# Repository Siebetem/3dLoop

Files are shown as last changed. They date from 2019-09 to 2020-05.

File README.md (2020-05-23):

# 3dLoop
## Intro
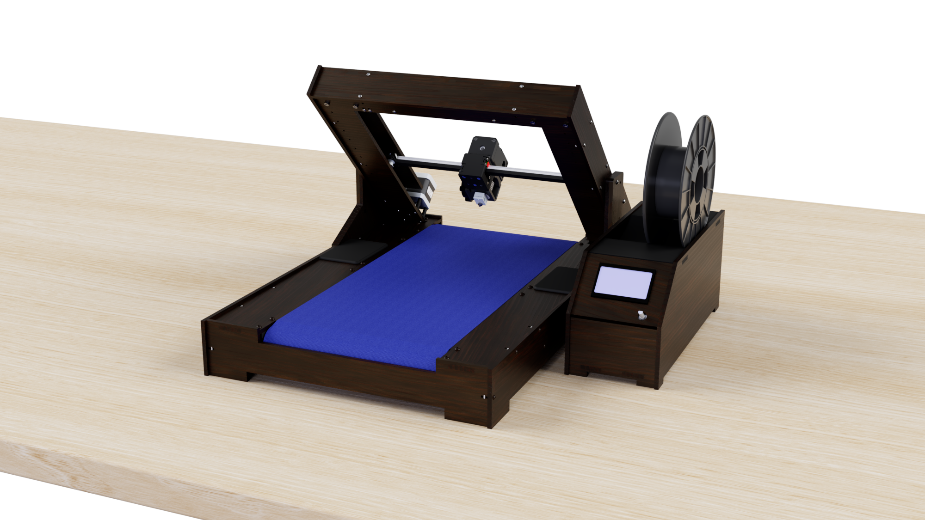
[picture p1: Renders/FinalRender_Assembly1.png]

3D printers are awesome machines, but they come with a variety of limitations:

First: printed objects are mostly small. Prints are always smaller than the printer itself. So if you want to make big prints, you need a big printer and even with this big printer are possibilities limited.

Second: When the printer is finished printing your object, human interaction is needed to proceed the next print. The printer isn’t able to remove the printed object and start a new one.

To produce parts fast and cost-effectively, I’ve designed a printer that can print many parts sequentially. Not only will it be more costeffective than other printers, it will be fairly easy to reproduce the printer with a minimal need of tools. I tried to make as many parts as possible with tools that are accessible in a FabLab/makerspace.

The printer uses a conveyor belt as print bed, whereas a normal printer uses a fixed build plate. A belt as printbed enables the printer to roll off the object and start printing a new object. This also makes it possible to make objects that are (almost) infinite in 1 direction.

There are 2 differtent configurations in which the printer can be configured.
I will describe the 2 differtent configurations separatly:

## Configuration 1 (Infinite printing)
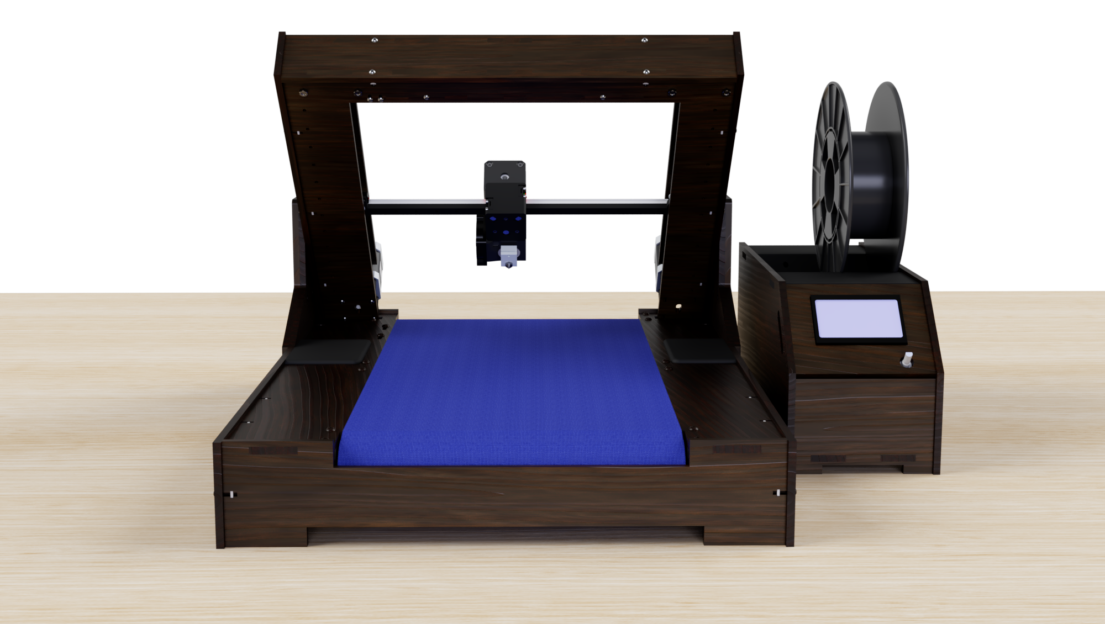
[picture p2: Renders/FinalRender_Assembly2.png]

In this configuration, It's possible to make objects with one infinite dimention.
The X,Y-assembly is oriented under an 45 degree angle towards the bed assembly.
This is especially usefull for extrusions, but it makes it also possible to print objects without support wereas normal printers would need support. For every layer, the bed system rols a bit further. In that way, objects can be bigger than the length of the belt.

## Configuration 2 (Normal 3D printer with automated object rejection)
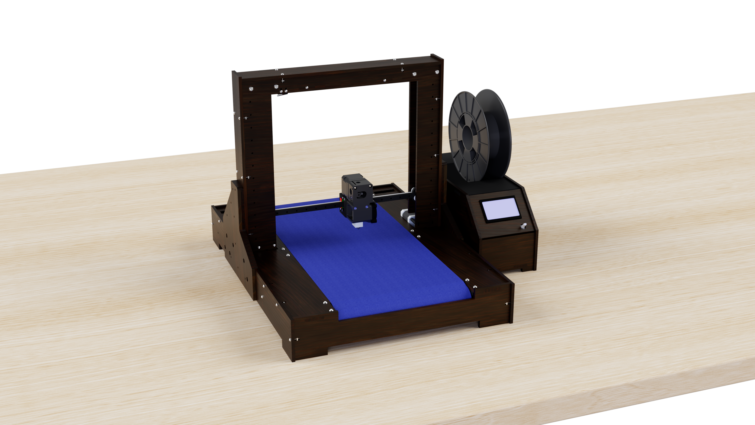
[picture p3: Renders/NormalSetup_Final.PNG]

This configuration give you all the advantages of the standard XYZ setup with the addition of automaticly rejection of the print. It makes it possible to print many objects, without the need of human interaction between diffrent objects. This is especially handy when you want to make a printfarm, or want to print many parts when you're away or sleeping.

The design makes it very easy to switch between the two configurations. The extruderassembly is magnetic detatchable. It's possible to attach the extruderassembly in 2 different orientations to the X-carriage.

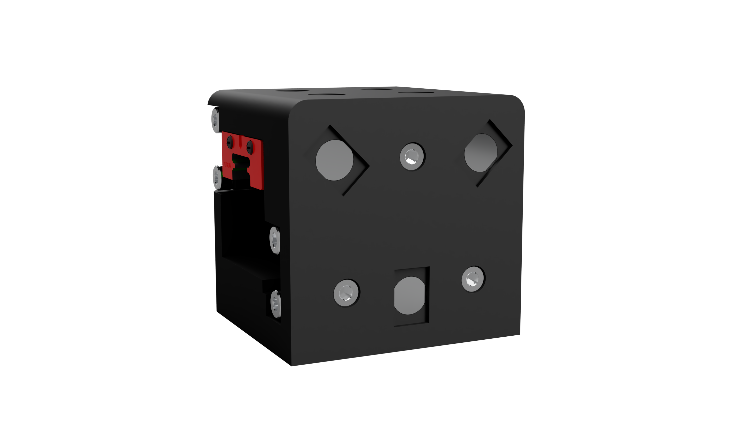
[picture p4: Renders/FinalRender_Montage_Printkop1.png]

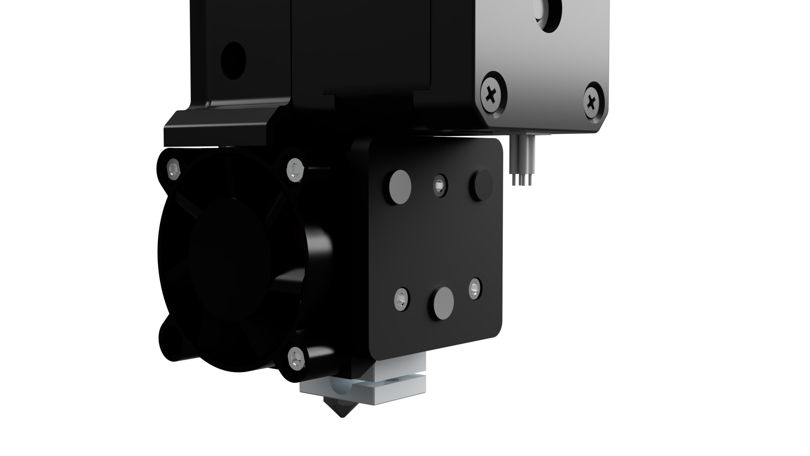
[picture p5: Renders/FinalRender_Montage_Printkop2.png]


The XY-axis assembly is easy detatchable from the Z-axis assembly by unscrewing 3 screws on each side.

By the use of two side pannels, the XY-as can be easely swichted between the two configurations. In the side pannels there are holes to mount the XY-axis vertically (Configuration 2) and under a 45 degree angle (Configuration 1).

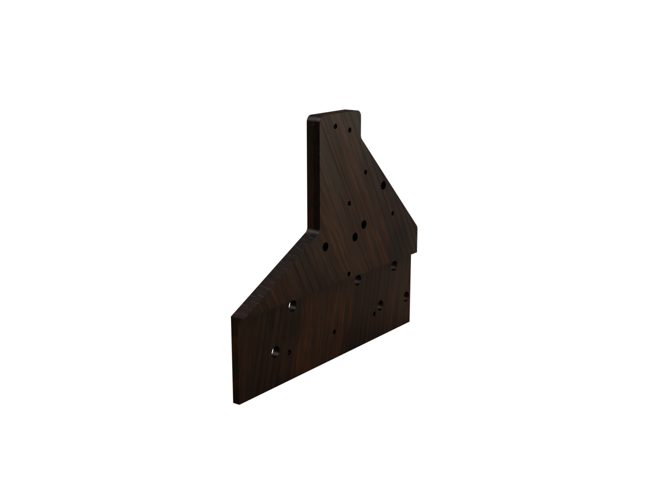
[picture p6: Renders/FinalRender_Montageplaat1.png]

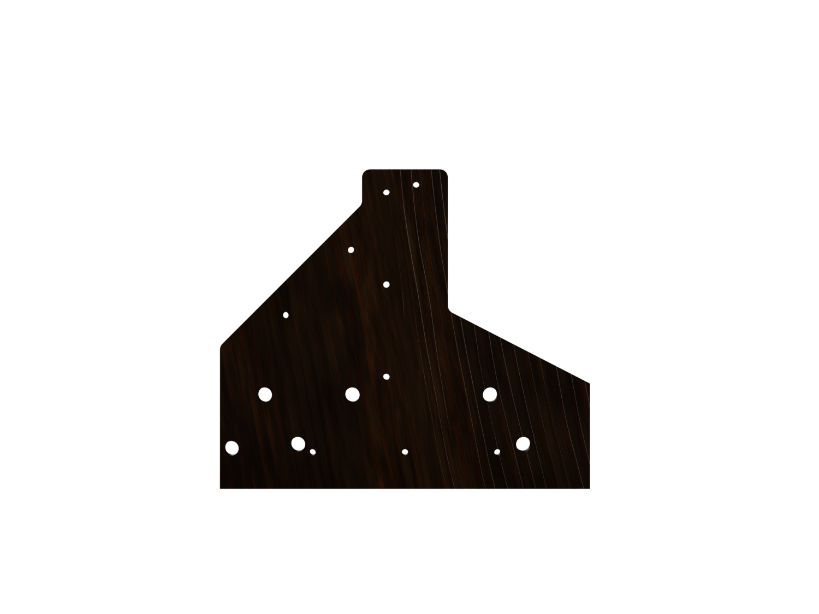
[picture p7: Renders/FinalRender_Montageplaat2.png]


## Electronic Box
The mainbord and powersupply are mounted inside a seperate unit, the electronic box.
The printer uses a MKS GEN 1.4 board, to run the Marlin firmware.
In the electronic box, there was special attention needed to the airflow, to prevent the closed box form overheating.
On the top of this box, there is a spoolholder.

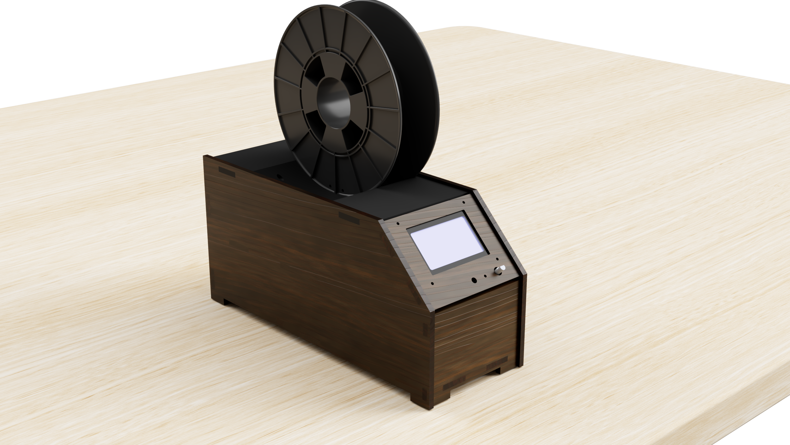
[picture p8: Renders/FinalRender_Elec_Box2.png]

On the back of the box, there are all the connectors for the differtent components. The use of connectors makes transportation of the printer easier.
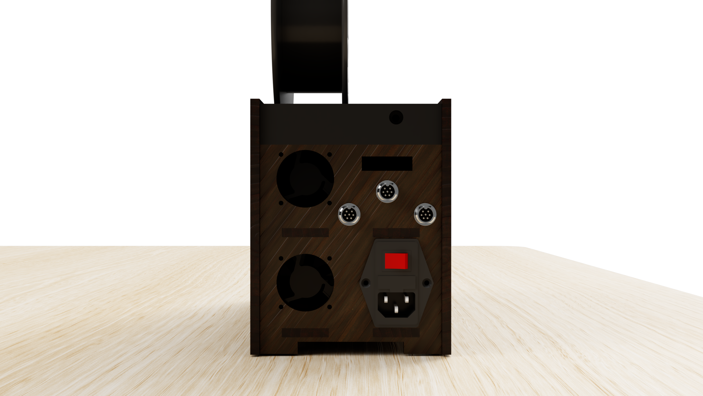
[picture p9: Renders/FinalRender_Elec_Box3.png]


##
This printer is fully custom made, every part is carefully designed to make sure the machine will work as good as possible.

On this Github page, you can find all the details about this printer. I share all the designfiles as well as software, firmware and used parts.

Don't hesitate to contact me or post a comment if you have any questions!

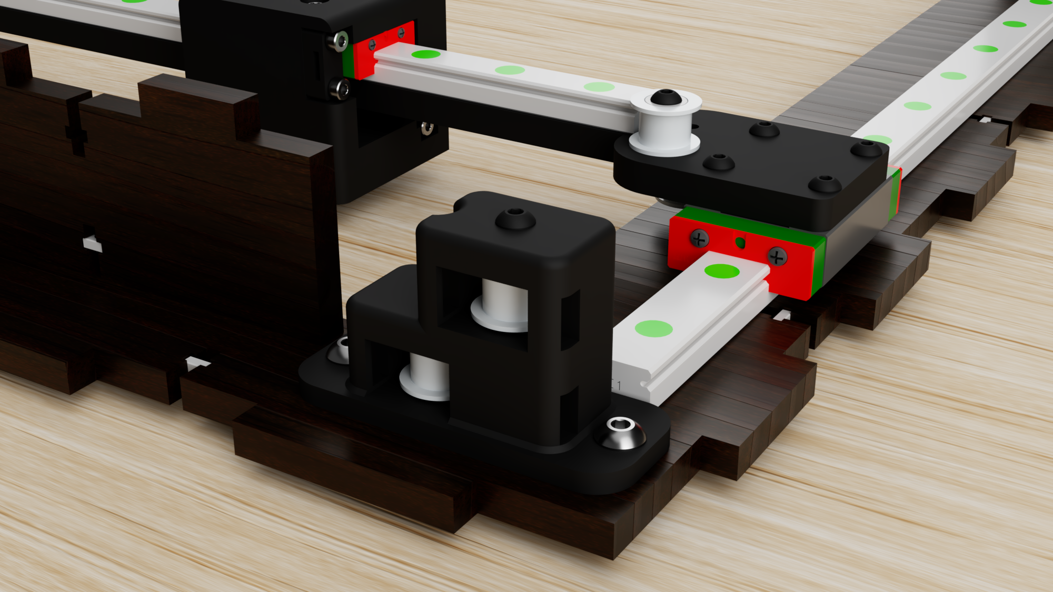
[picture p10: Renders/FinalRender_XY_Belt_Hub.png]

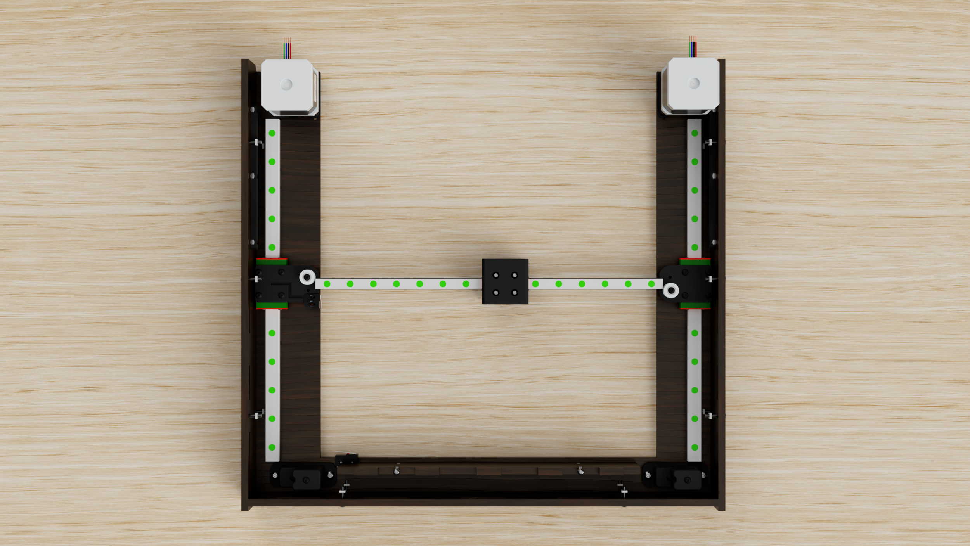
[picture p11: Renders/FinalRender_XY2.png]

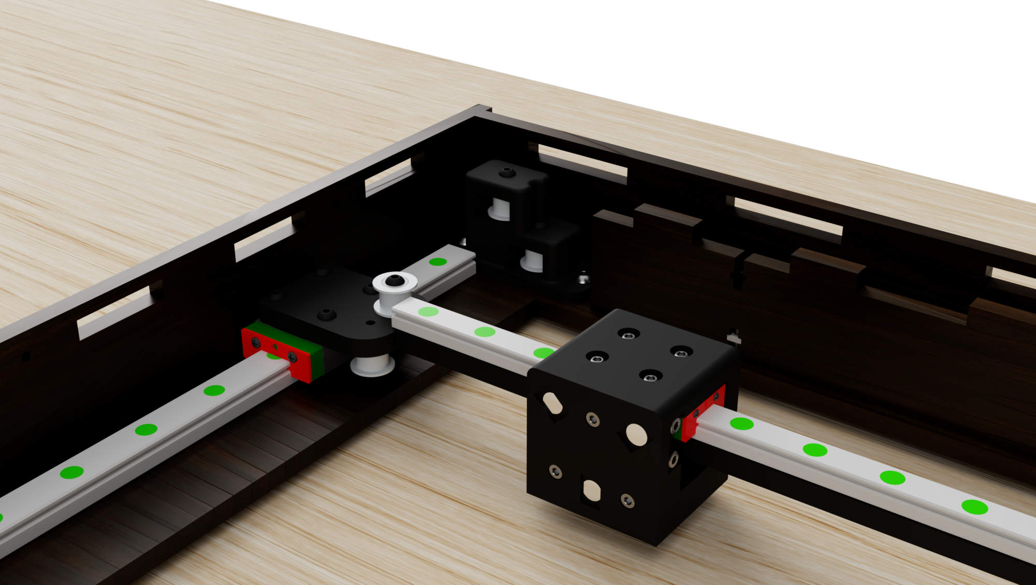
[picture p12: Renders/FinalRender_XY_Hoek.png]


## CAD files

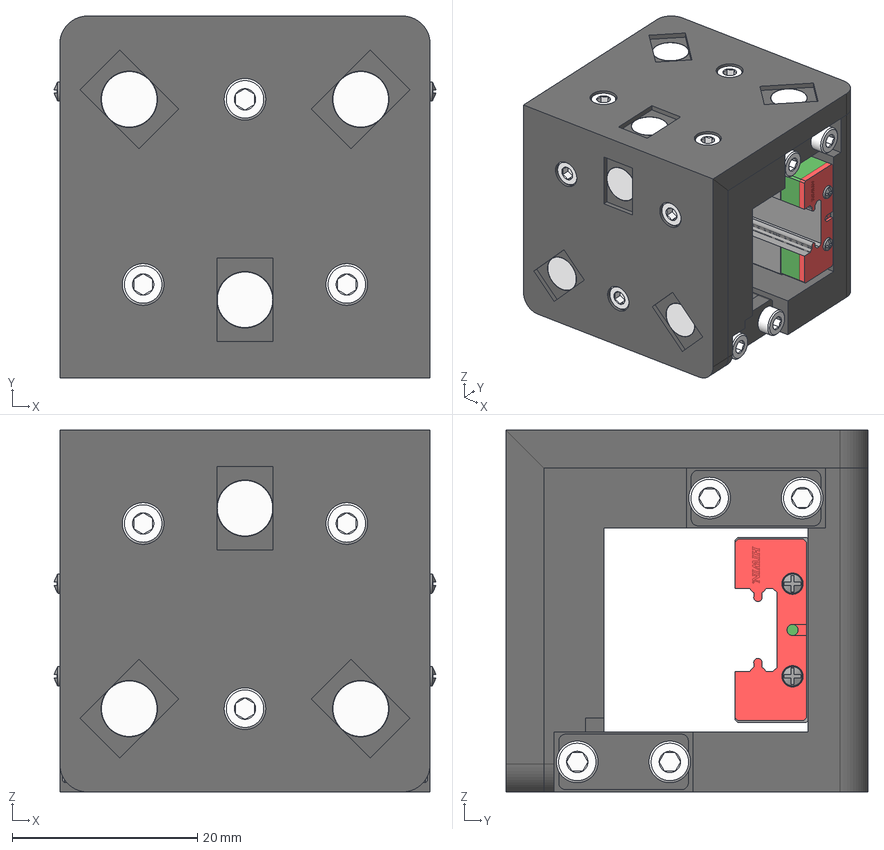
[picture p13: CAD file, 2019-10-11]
CAD_Files/3D_Files/XY-Axis/STEP_Files/Carriage_Assembly v25.step
41.3 x 39.1 x 39.1 mm
MGN09H_ZF_H_M_SS_FILE_1
Magnet x 6
M2.5x5 x 6
M2.5x10 x 8
M3x6 x 4

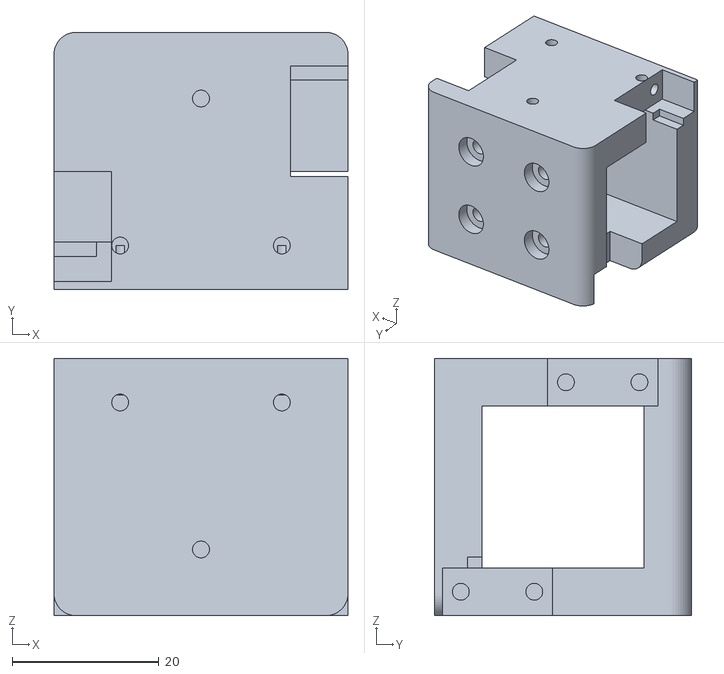
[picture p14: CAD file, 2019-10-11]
CAD_Files/3D_Files/XY-Axis/STL_Files/Carriage_Assembly v26.stl
40.0 x 35.0 x 35.0

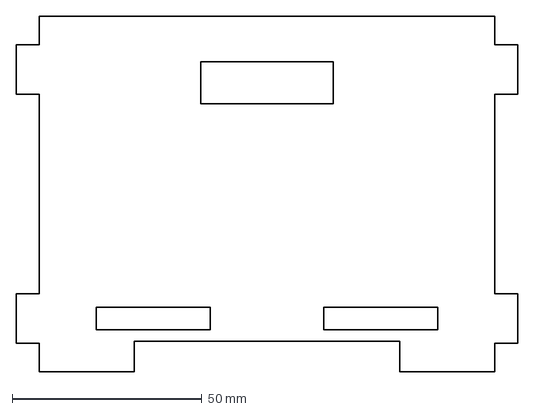
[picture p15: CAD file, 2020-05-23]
CAD_Files/2D_Files/ControllerBox/ControllerBox_Front_SD.dxf
132.0 x 93.6 mm

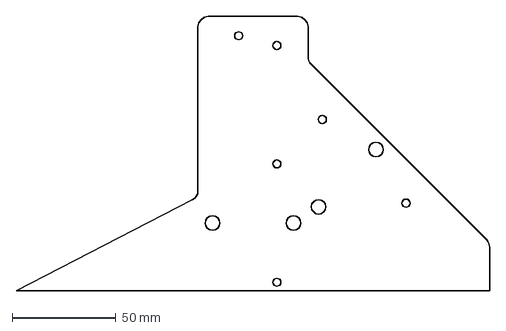
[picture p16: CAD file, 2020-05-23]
CAD_Files/2D_Files/MountingPlate/MountingPlate2.dxf
228.0 x 132.0 mm

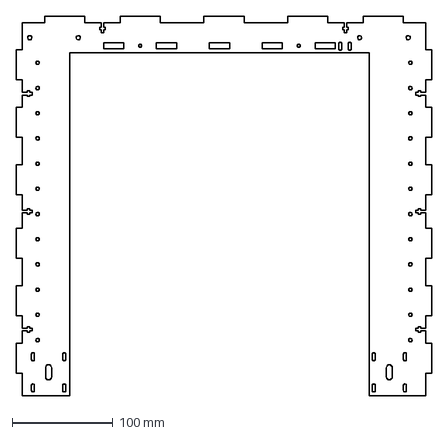
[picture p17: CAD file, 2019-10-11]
CAD_Files/2D_Files/XY-Axis/XY-Axis_Bottem.dxf
412.0 x 376.0 mm

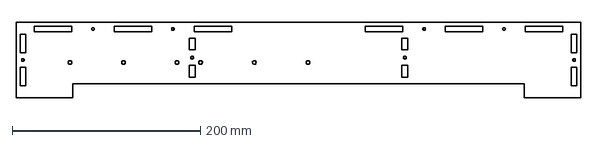
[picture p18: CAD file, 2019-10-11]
CAD_Files/2D_Files/Z-Axis/Z-Axis_Bed_Side.dxf
600.0 x 80.0 mm

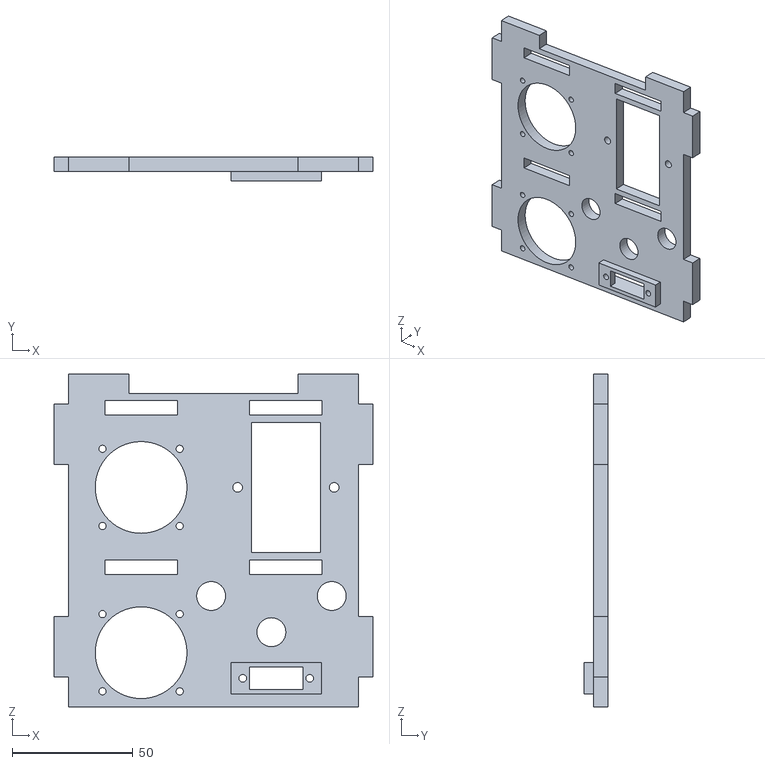
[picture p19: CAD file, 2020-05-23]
CAD_Files/3D_Files/ControllerBox/Back.stl
132.0 x 10.0 x 138.0

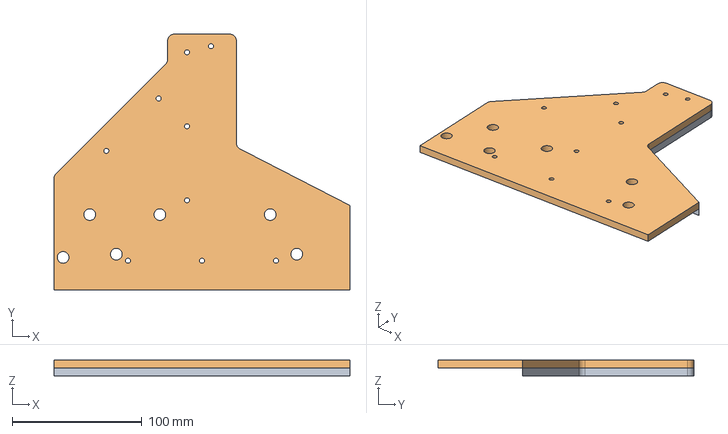
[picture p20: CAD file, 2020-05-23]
CAD_Files/3D_Files/MountingPlate/MountingPlate_v37.step
228.0 x 197.0 x 12.0 mm

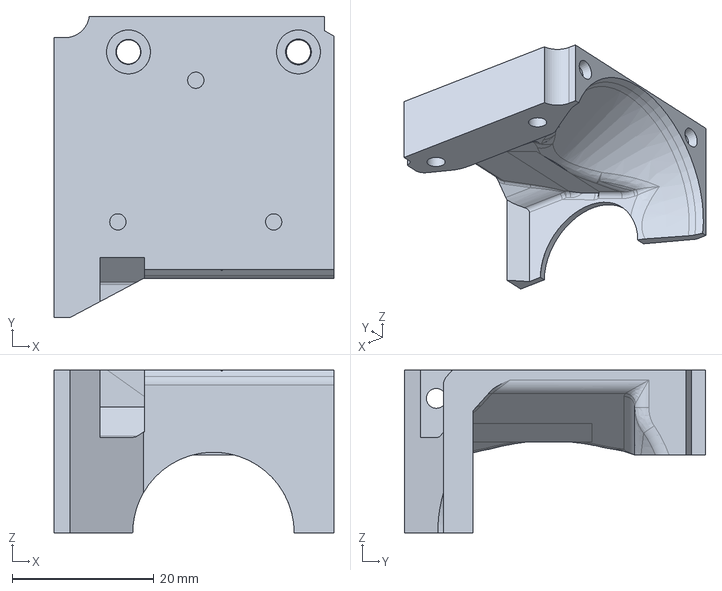
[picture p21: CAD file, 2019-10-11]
CAD_Files/3D_Files/Printhead/STEP_Files/Extruder_Cover v13.step
39.5 x 42.5 x 23.0 mm

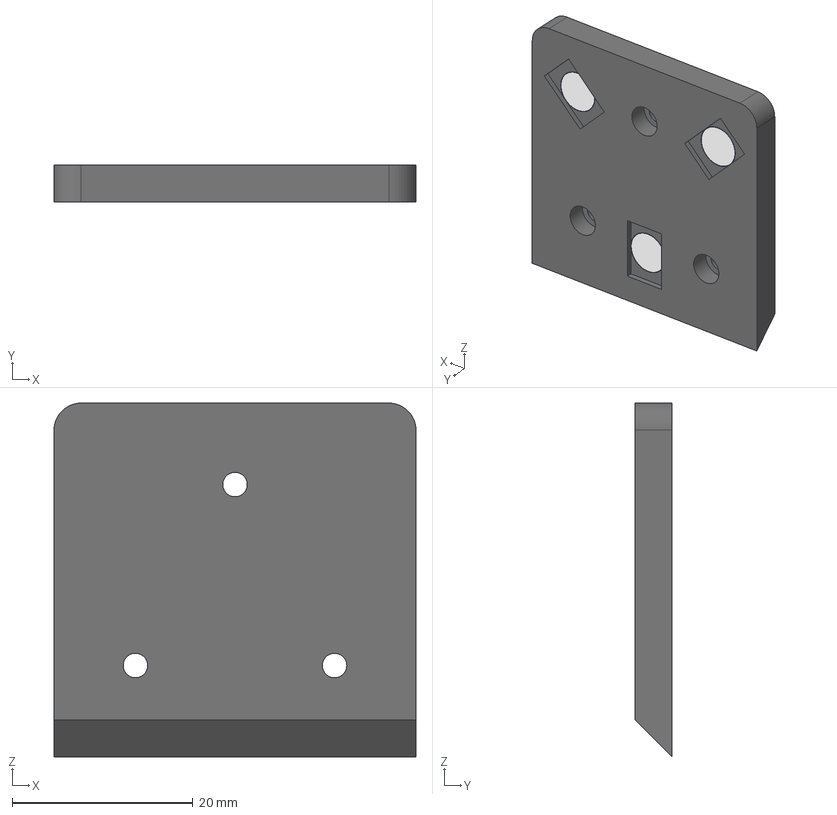
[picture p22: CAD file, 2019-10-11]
CAD_Files/3D_Files/XY-Axis/STEP_Files/MountingPlate_Carriage v14.step
40.0 x 4.10 x 39.1 mm
Magnet x 3

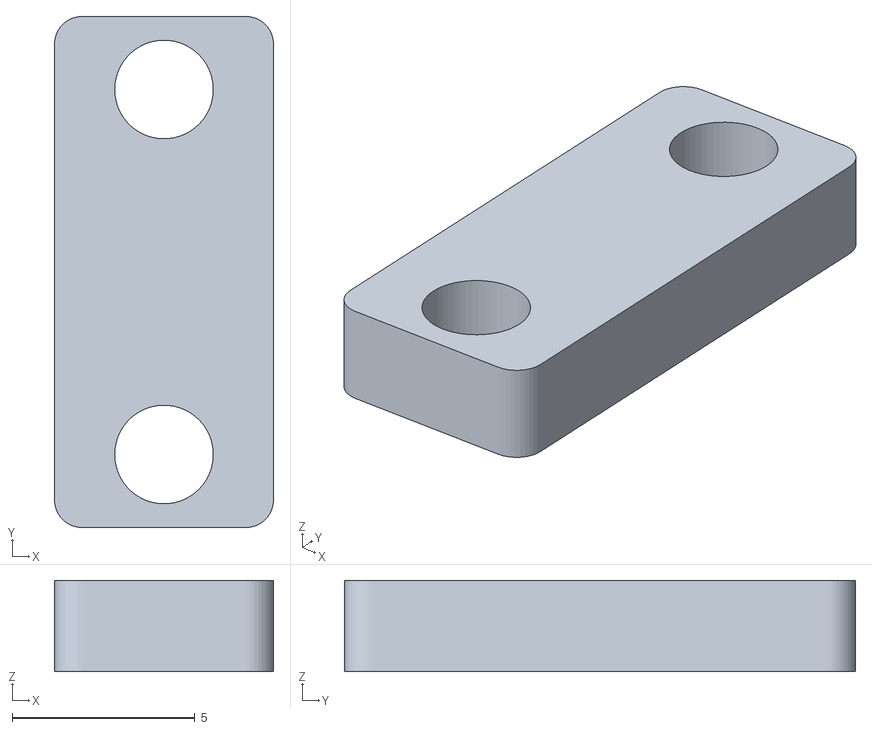
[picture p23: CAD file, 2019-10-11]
CAD_Files/3D_Files/XY-Axis/STL_Files/Belt_Clamp2 v13.stl
6.00 x 14.0 x 2.50

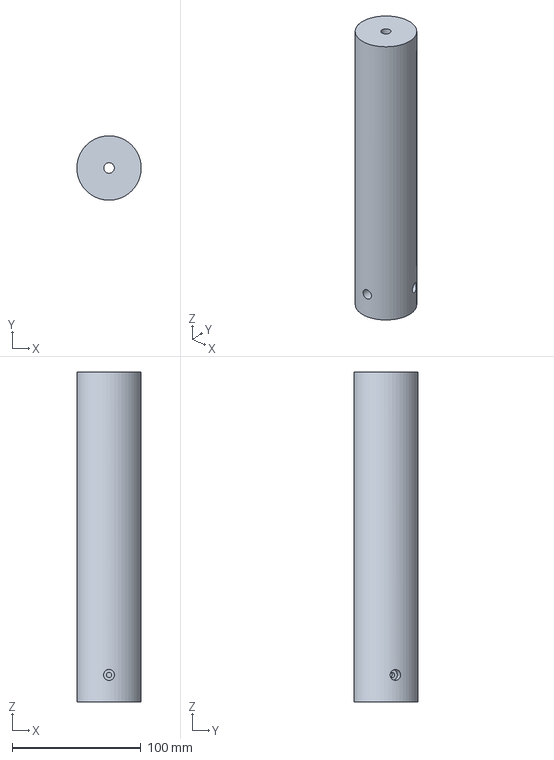
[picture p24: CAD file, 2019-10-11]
CAD_Files/3D_Files/Z-Axis/STEP_Files/Rol_Motor v10.step
50.0 x 50.0 x 256.0 mm

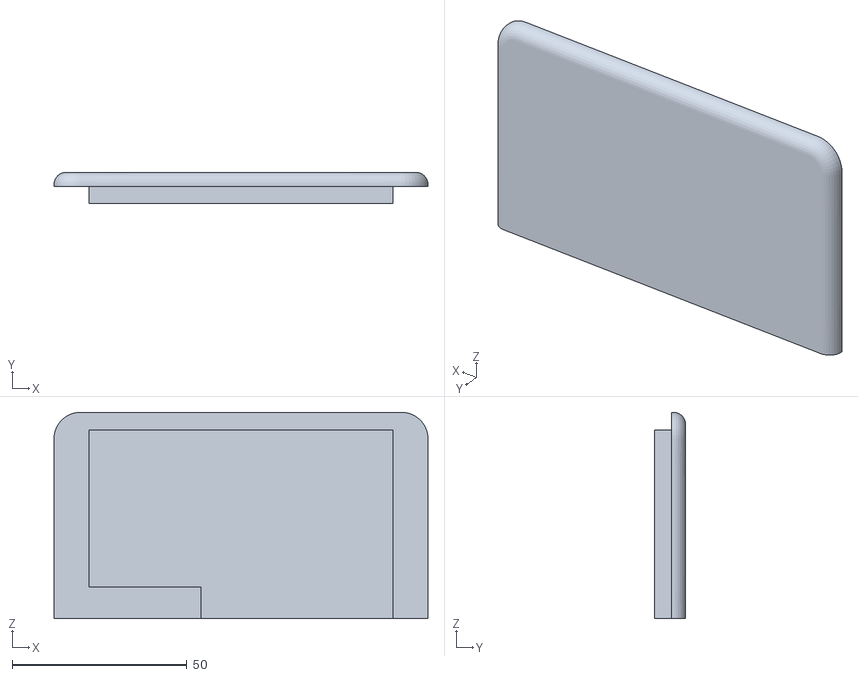
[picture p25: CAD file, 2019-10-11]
CAD_Files/3D_Files/Z-Axis/STL_Files/Plate1 v5.stl
107.0 x 9.00 x 59.0

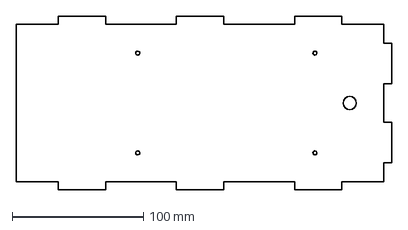
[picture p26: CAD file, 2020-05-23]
CAD_Files/2D_Files/ControllerBox/ControllerBox_Inside.dxf
286.0 x 132.0 mm

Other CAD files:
CAD_Files/2D_Files/MountingPlate/MountingPlate1.dxf
CAD_Files/2D_Files/XY-Axis/XY-Axis_Front.dxf
CAD_Files/2D_Files/Z-Axis/Z-Axis_Front:Back.dxf
CAD_Files/3D_Files/ControllerBox/Top.stl
CAD_Files/2D_Files/ControllerBox/ControllerBox_Bottom.dxf
CAD_Files/2D_Files/ControllerBox/ControllerBox_Front_Display.dxf
CAD_Files/2D_Files/ControllerBox/ControllerBox_Side.dxf
CAD_Files/2D_Files/XY-Axis/XY-Axis_Side.dxf
CAD_Files/2D_Files/XY-Axis/XY-Axis_Support.dxf
CAD_Files/2D_Files/XY-Axis/XY-Axis_Top.dxf
CAD_Files/2D_Files/Z-Axis/Z-Axis_Bed_Support.dxf
CAD_Files/2D_Files/Z-Axis/Z-Axis_Bed_Top.dxf
CAD_Files/3D_Files/MountingPlate/MountingPlate_v38.f3d
CAD_Files/3D_Files/Printhead/F3D_Files/Extruder_Body v13.f3d
CAD_Files/3D_Files/Printhead/F3D_Files/Extruder_Cover v13.f3d
CAD_Files/3D_Files/Printhead/F3D_Files/Extruder_Idler v1.f3d
CAD_Files/3D_Files/Printhead/F3D_Files/Extruder_Motor_Plate v6.f3d
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

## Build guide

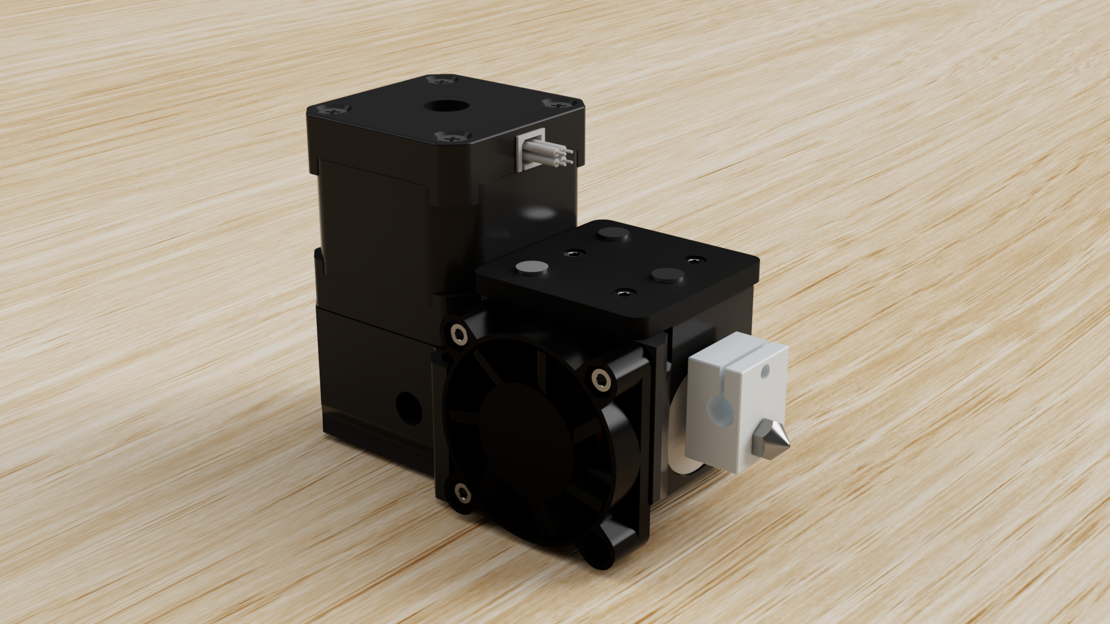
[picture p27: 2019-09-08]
Renders/FinalRender_Printhead2.png

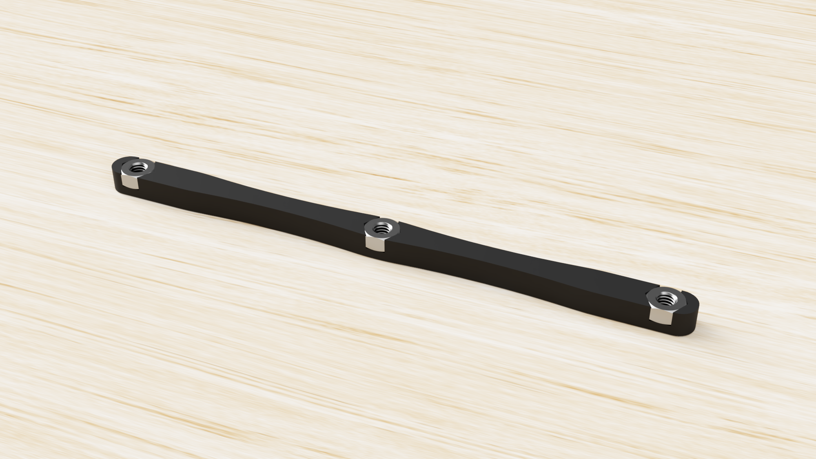
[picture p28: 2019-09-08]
Renders/FinalRender_Montage.png

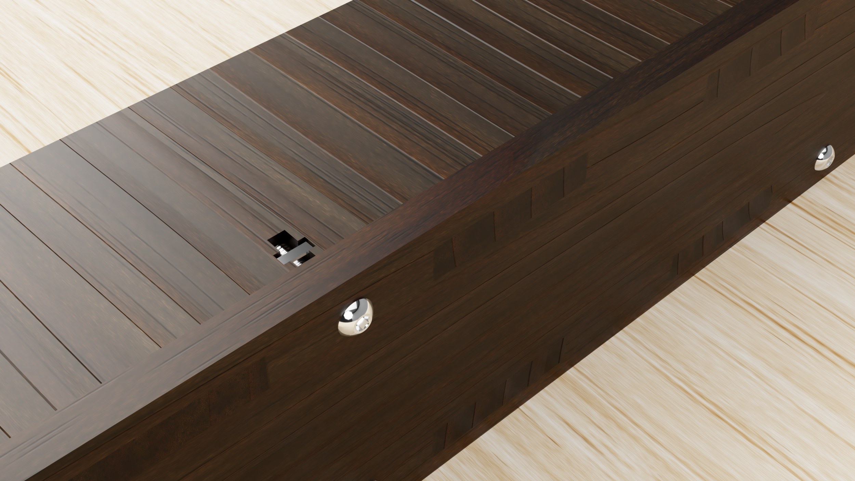
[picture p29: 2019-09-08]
Renders/FinalRender_XY_Montage2.png

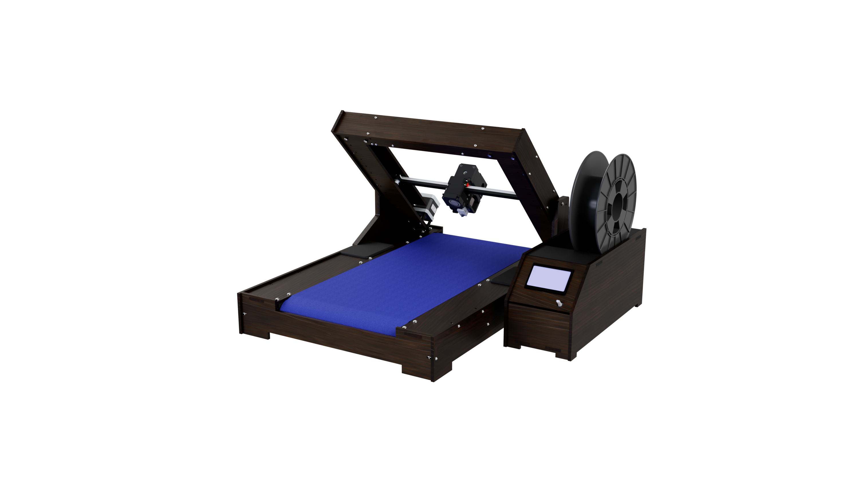
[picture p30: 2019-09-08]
Renders/FinalRender_Assembly6.PNG

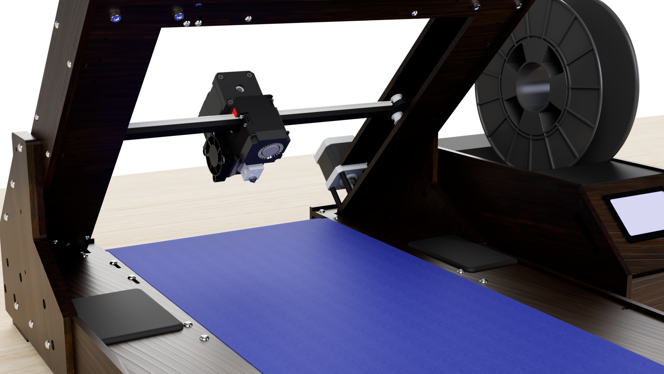
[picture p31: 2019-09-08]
Renders/FinalRender_Assembly5.png

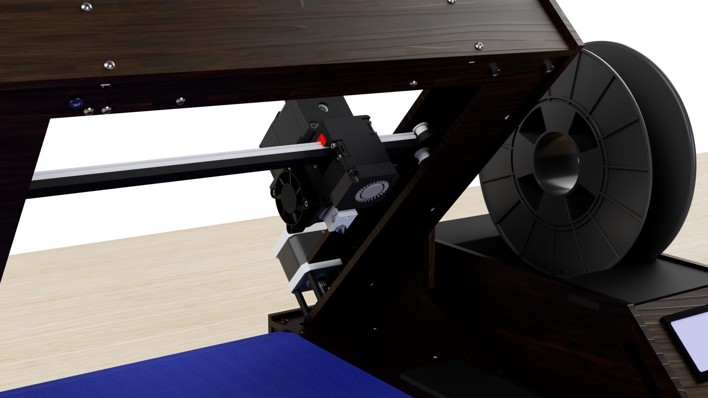
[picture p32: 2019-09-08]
Renders/FinalRender_Assembly3.png

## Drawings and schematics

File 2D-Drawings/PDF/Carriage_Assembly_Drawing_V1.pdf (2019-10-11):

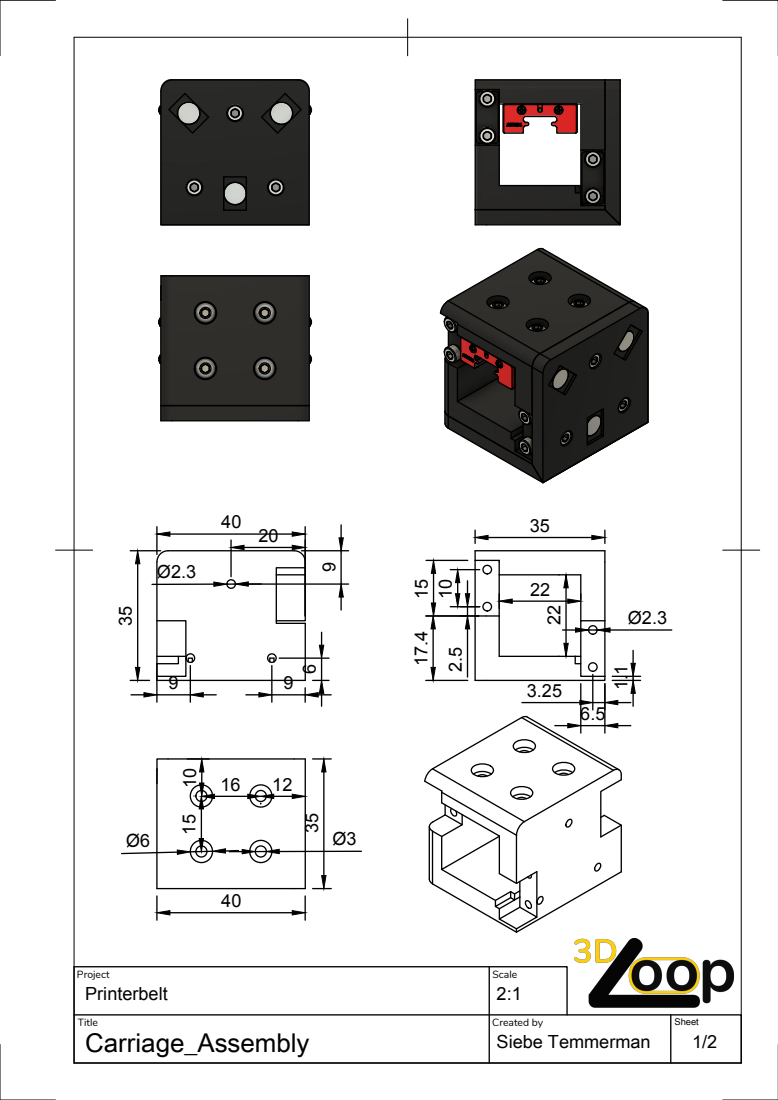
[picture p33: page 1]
Printerbelt

Project | Scale

Title Carriage_Assembly | Created by Siebe Temmerman | Sheet 1/2

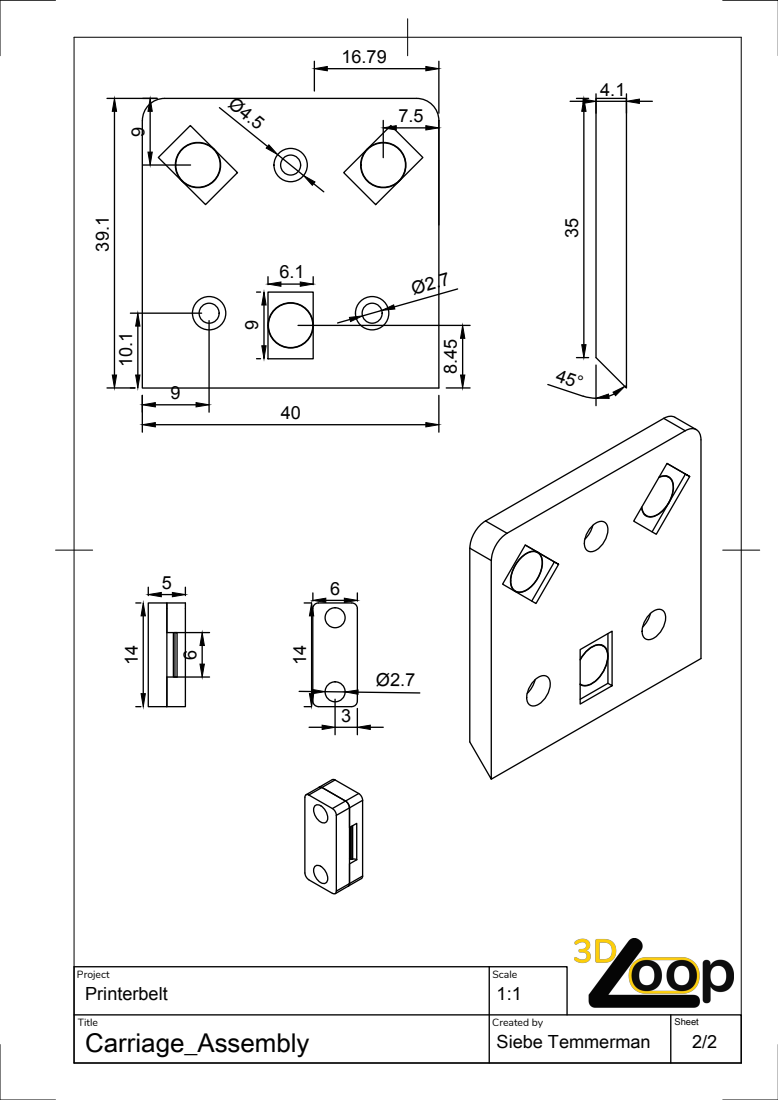
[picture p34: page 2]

Project Printerbelt | Scale 1:1

Title Carriage_Assembly | Created by Siebe Temmerman | Sheet 2/2

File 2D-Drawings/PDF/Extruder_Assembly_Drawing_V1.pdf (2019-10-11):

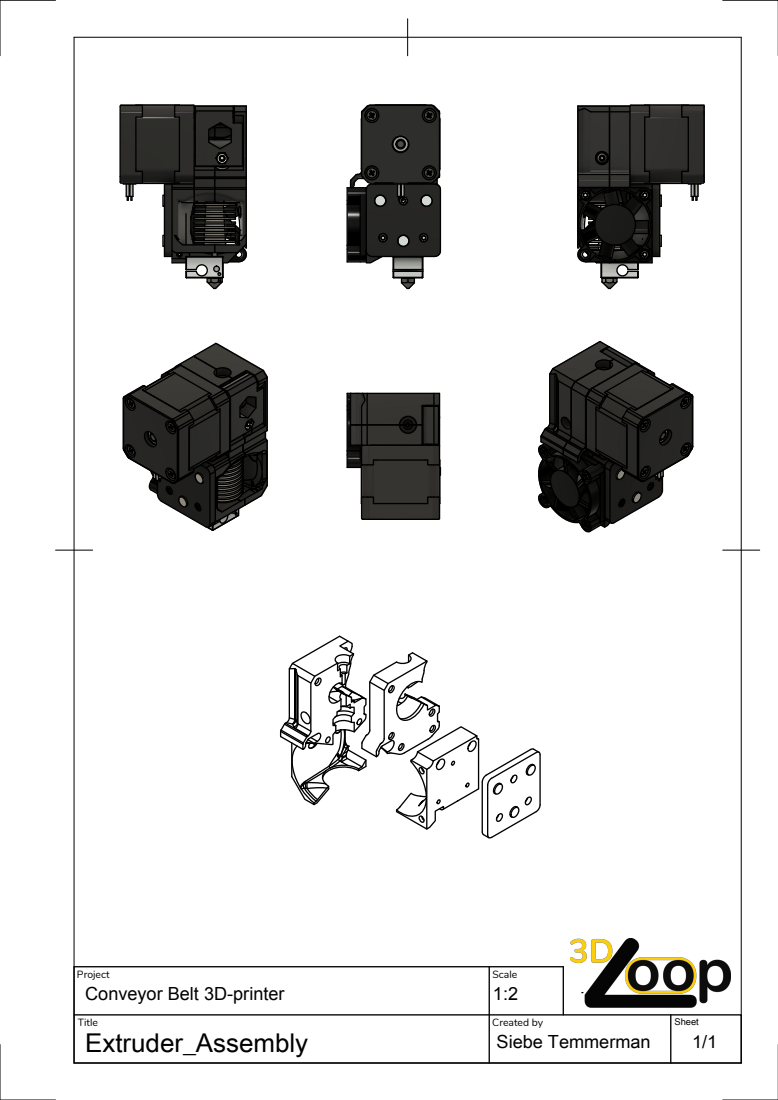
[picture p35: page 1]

Project Conveyor Belt 3D-printer | Scale 1:2

Title Extruder_Assembly | Created by Siebe Temmerman | Sheet 1/1

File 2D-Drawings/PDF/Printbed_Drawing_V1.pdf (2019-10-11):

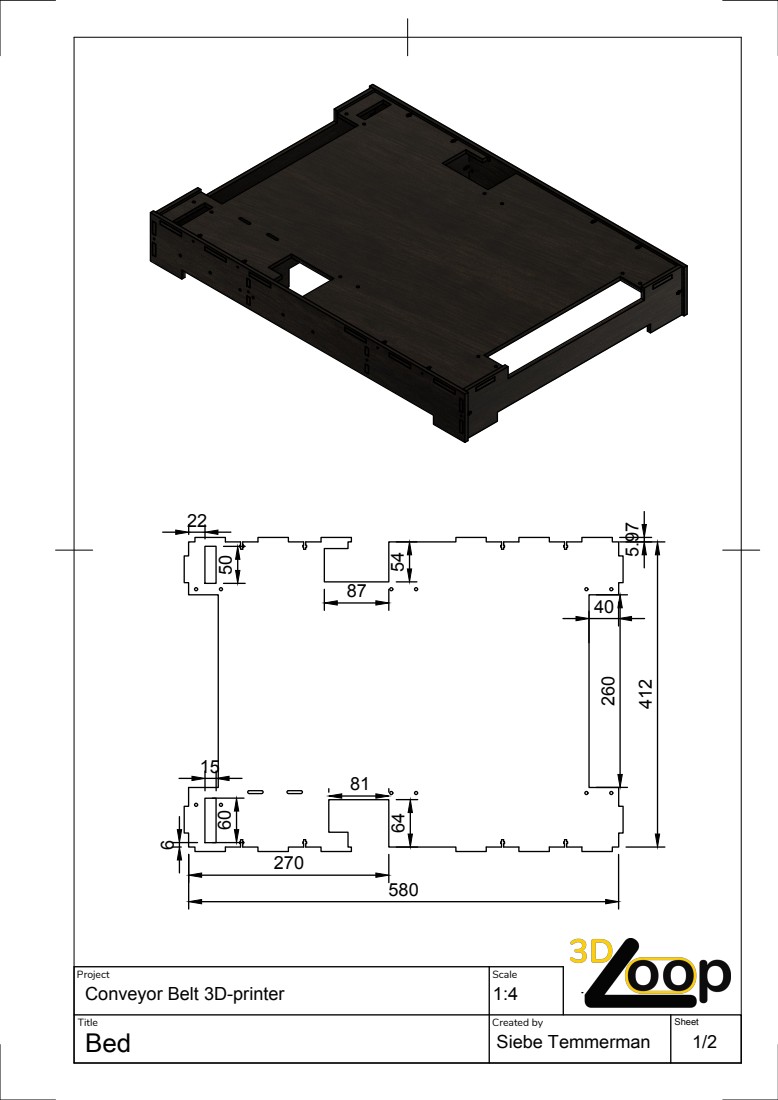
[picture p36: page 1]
Conveyor Belt 3D-printer

Project | Scale

Title Bed | Created by Siebe Temmerman | Sheet 1/2

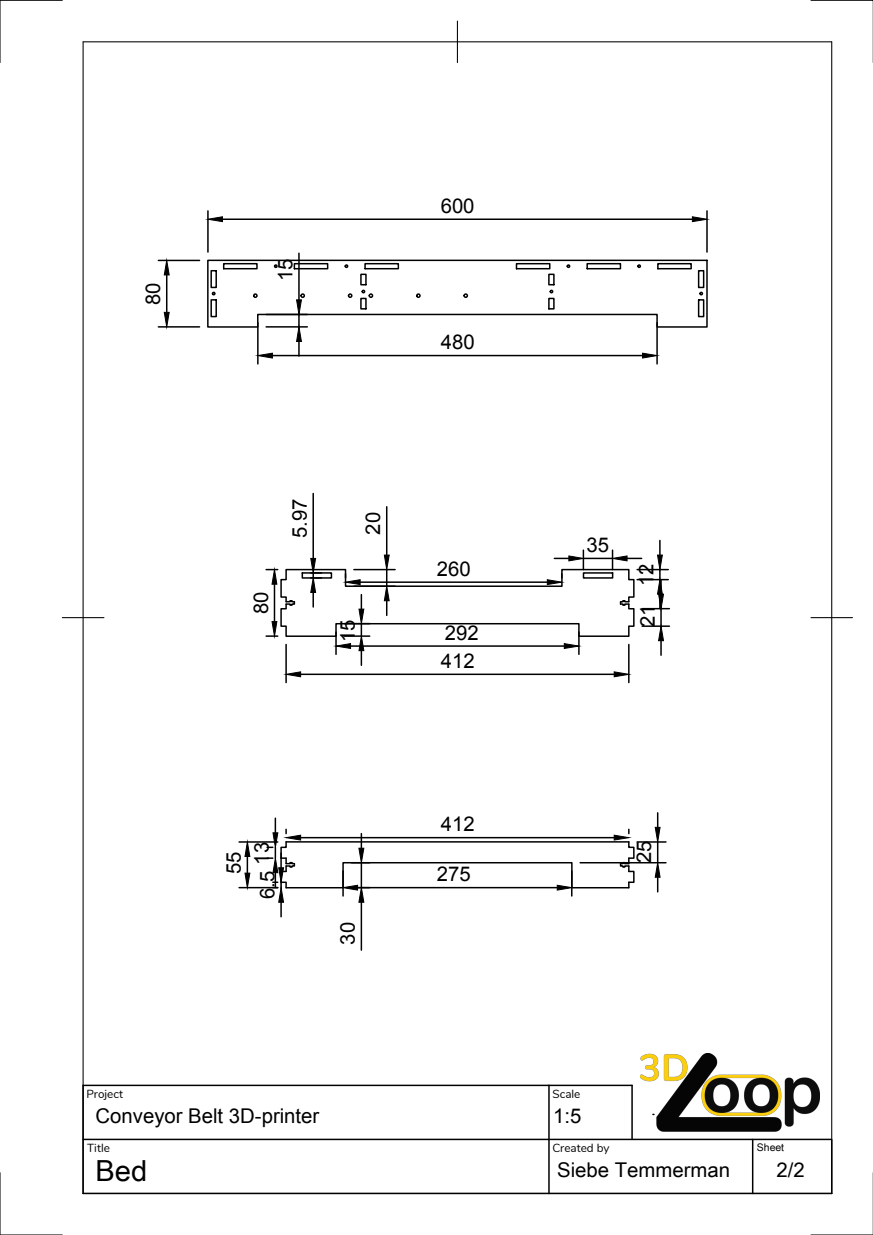
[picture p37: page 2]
Conveyor Belt 3D-printer

Project | Scale

Title Bed | Created by Siebe Temmerman | Sheet 2/2

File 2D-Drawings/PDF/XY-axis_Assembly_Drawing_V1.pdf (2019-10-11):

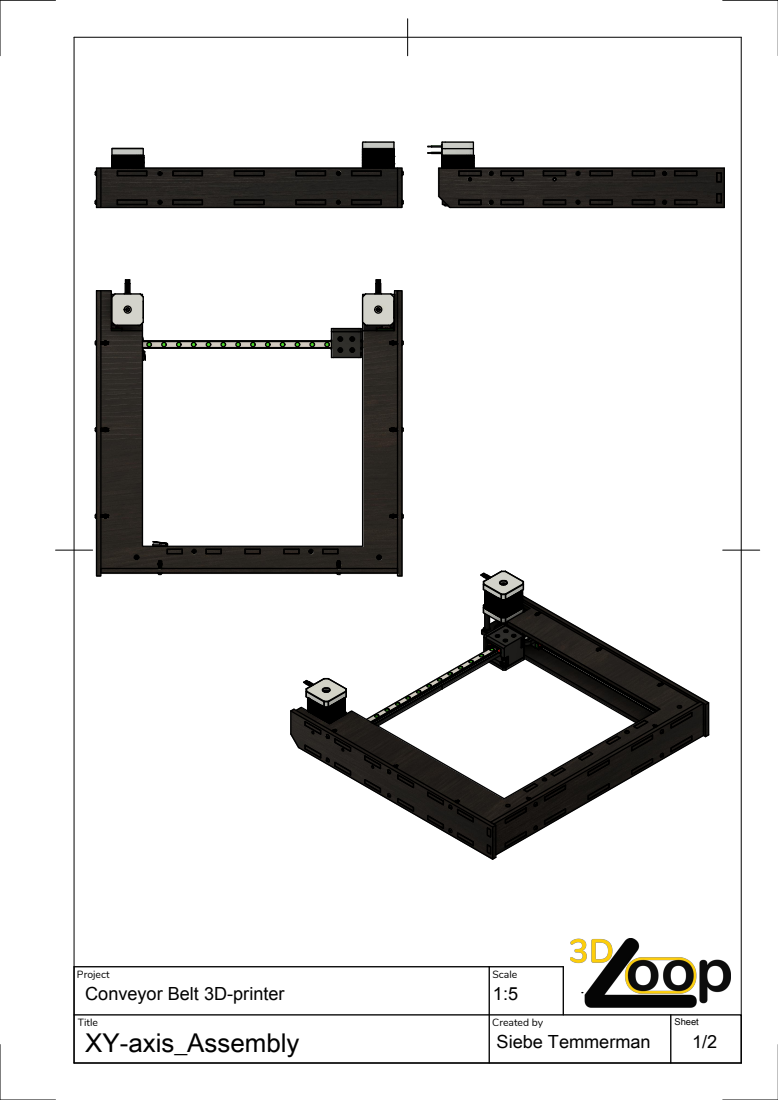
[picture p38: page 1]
Title; Created by; XY-axis_Assembly; Siebe Temmerman; Conveyor Belt 3D-printer

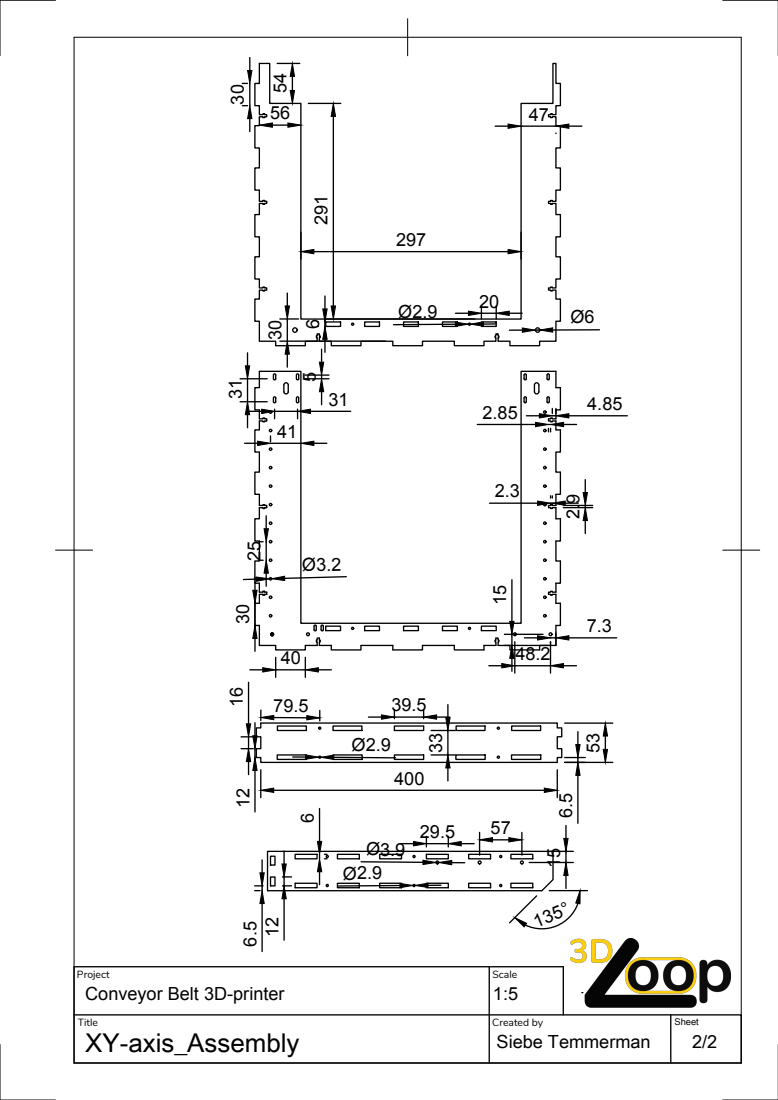
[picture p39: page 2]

Project Conveyor Belt 3D-printer | Scale 1:5

Title XY-axis_Assembly | Created by Siebe Temmerman | Sheet 2/2

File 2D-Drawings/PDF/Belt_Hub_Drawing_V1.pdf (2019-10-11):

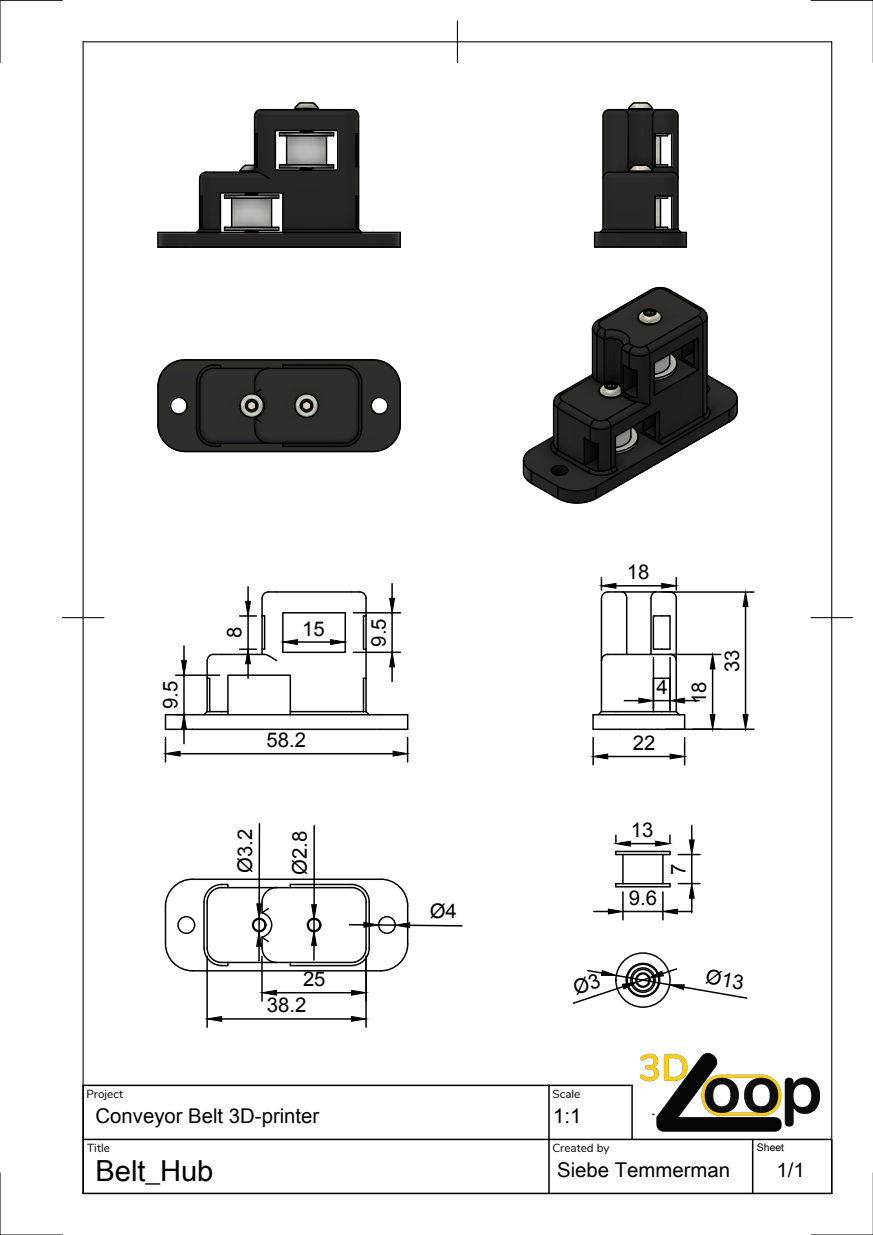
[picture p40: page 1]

Project Conveyor Belt 3D-printer | Scale 1:1

Title Belt_Hub | Created by Siebe Temmerman | Sheet 1/1

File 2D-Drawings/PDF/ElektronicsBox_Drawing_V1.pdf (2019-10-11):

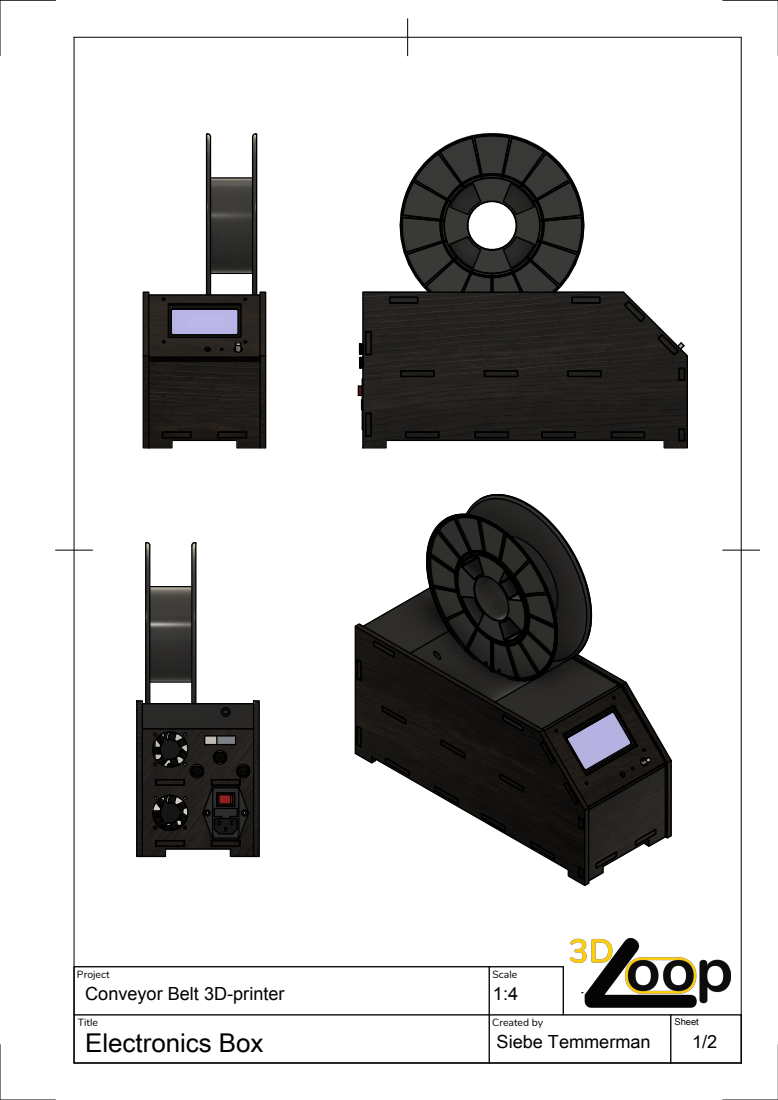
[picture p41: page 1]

Project Conveyor Belt 3D-printer | Scale 1:4

Title Electronics Box | Created by Siebe Temmerman | Sheet 1/2

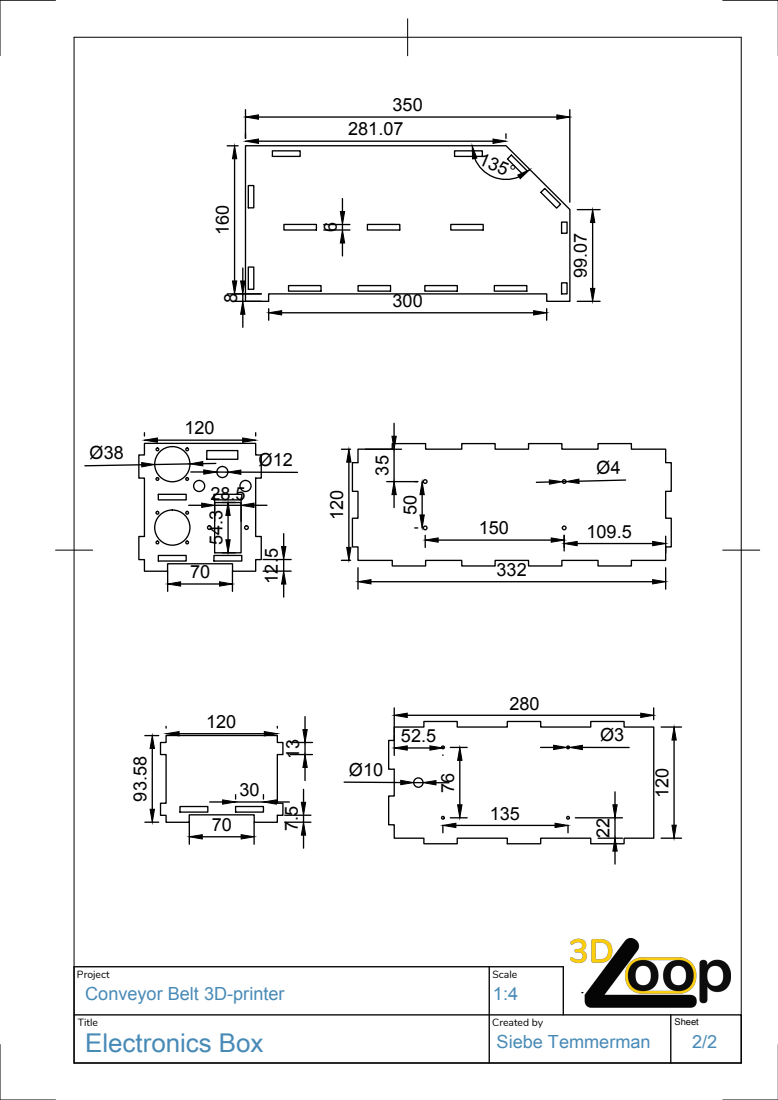
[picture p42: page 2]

Project Conveyor Belt 3D-printer | Scale 1:4

Title Electronics Box | Created by Siebe Temmerman | Sheet 2/2

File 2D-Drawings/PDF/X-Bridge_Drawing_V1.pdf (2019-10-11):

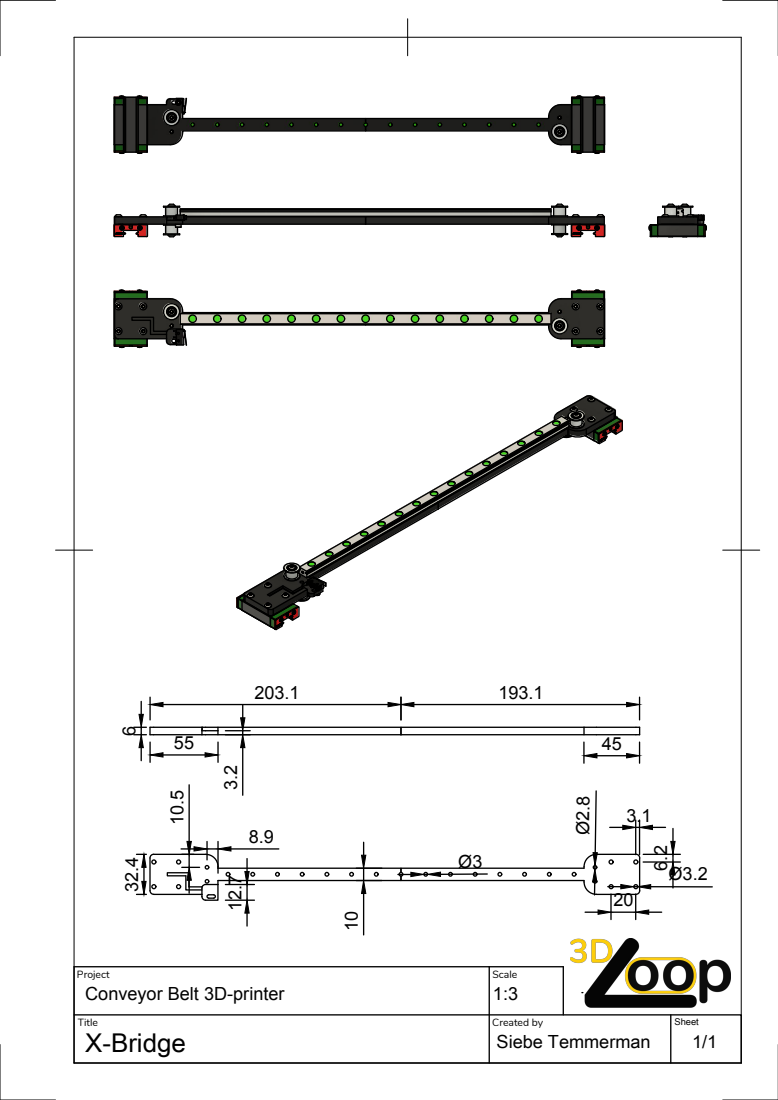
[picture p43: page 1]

Project Conveyor Belt 3D-printer | Scale 1:3

Title X-Bridge | Created by Siebe Temmerman | Sheet 1/1

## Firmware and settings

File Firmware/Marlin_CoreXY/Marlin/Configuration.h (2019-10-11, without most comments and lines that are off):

#include <U8glib.h>
#define CONFIGURATION_H
#define CONFIGURATION_H_VERSION 010109
#define STRING_CONFIG_H_AUTHOR "(none, default config)" // Who made the changes.
#define SHOW_BOOTSCREEN
#define STRING_SPLASH_LINE1 SHORT_BUILD_VERSION // will be shown during bootup in line 1
#define STRING_SPLASH_LINE2 WEBSITE_URL         // will be shown during bootup in line 2
#define SERIAL_PORT 0
#define BAUDRATE 250000
  #define MOTHERBOARD BOARD_MKS_GEN_13
#define EXTRUDERS 1
#define DEFAULT_NOMINAL_FILAMENT_DIA 1,75
#define POWER_SUPPLY 0
#define TEMP_SENSOR_0 5
#define TEMP_SENSOR_1 0
#define TEMP_SENSOR_2 0
#define TEMP_SENSOR_3 0
#define TEMP_SENSOR_4 0
#define TEMP_SENSOR_BED 0
#define TEMP_SENSOR_CHAMBER 0
#define DUMMY_THERMISTOR_998_VALUE 25
#define DUMMY_THERMISTOR_999_VALUE 100
#define MAX_REDUNDANT_TEMP_SENSOR_DIFF 10
#define TEMP_RESIDENCY_TIME 10  // (seconds)
#define TEMP_HYSTERESIS 3       // (degC) range of +/- temperatures considered "close" to the target one
#define TEMP_WINDOW     1       // (degC) Window around target to start the residency timer x degC early.
#define TEMP_BED_RESIDENCY_TIME 10  // (seconds)
#define TEMP_BED_HYSTERESIS 3       // (degC) range of +/- temperatures considered "close" to the target one
#define TEMP_BED_WINDOW     1       // (degC) Window around target to start the residency timer x degC early.
#define HEATER_0_MINTEMP 5
#define HEATER_1_MINTEMP 5
#define HEATER_2_MINTEMP 5
#define HEATER_3_MINTEMP 5
#define HEATER_4_MINTEMP 5
#define BED_MINTEMP 5
#define HEATER_0_MAXTEMP 275
#define HEATER_1_MAXTEMP 275
#define HEATER_2_MAXTEMP 275
#define HEATER_3_MAXTEMP 275
#define HEATER_4_MAXTEMP 275
#define BED_MAXTEMP 150
#define PIDTEMP
#define BANG_MAX 255     // Limits current to nozzle while in bang-bang mode; 255=full current
#define PID_MAX BANG_MAX // Limits current to nozzle while PID is active (see PID_FUNCTIONAL_RANGE below); 255=full current
#define PID_K1 0.95      // Smoothing factor within any PID loop
  #define PID_FUNCTIONAL_RANGE 10 // If the temperature difference between the target temperature and the actual temperature
#define DEFAULT_Kp 19.94
#define DEFAULT_Ki 3.25
#define DEFAULT_Kd 30.63
#define MAX_BED_POWER 255 // limits duty cycle to bed; 255=full current
#define PREVENT_COLD_EXTRUSION
#define EXTRUDE_MINTEMP 170
#define PREVENT_LENGTHY_EXTRUDE
#define EXTRUDE_MAXLENGTH 200
#define THERMAL_PROTECTION_HOTENDS // Enable thermal protection for all extruders
#define THERMAL_PROTECTION_BED     // Enable thermal protection for the heated bed
#define COREXY
#define USE_XMIN_PLUG
#define USE_YMAX_PLUG
#define USE_ZMAX_PLUG
#define ENDSTOPPULLUPS
#define X_MIN_ENDSTOP_INVERTING true // set to true to invert the logic of the endstop.
#define Y_MIN_ENDSTOP_INVERTING true // set to true to invert the logic of the endstop.
#define Z_MIN_ENDSTOP_INVERTING true // set to true to invert the logic of the endstop.
#define X_MAX_ENDSTOP_INVERTING true // set to true to invert the logic of the endstop.
#define Y_MAX_ENDSTOP_INVERTING true // set to true to invert the logic of the endstop.
#define Z_MAX_ENDSTOP_INVERTING true // set to true to invert the logic of the endstop.
#define Z_MIN_PROBE_ENDSTOP_INVERTING true // set to true to invert the logic of the probe.
#define ENDSTOP_NOISE_FILTER
#define DEFAULT_AXIS_STEPS_PER_UNIT   { 80, 80, 36, 161.3 }
#define DEFAULT_MAX_FEEDRATE          { 300, 300, 150, 40 }
#define DEFAULT_MAX_ACCELERATION      { 3000, 3000, 500, 10000 }
#define DEFAULT_ACCELERATION          1000    // X, Y, Z and E acceleration for printing moves
#define DEFAULT_RETRACT_ACCELERATION  3000    // E acceleration for retracts
#define DEFAULT_TRAVEL_ACCELERATION   1000    // X, Y, Z acceleration for travel (non printing) moves
#define DEFAULT_XJERK                 10.0
#define DEFAULT_YJERK                 10.0
#define DEFAULT_ZJERK                  0.3
#define DEFAULT_EJERK                  5.0
#define Z_MIN_PROBE_USES_Z_MIN_ENDSTOP_PIN
#define X_PROBE_OFFSET_FROM_EXTRUDER 10  // X offset: -left  +right  [of the nozzle]
#define Y_PROBE_OFFSET_FROM_EXTRUDER 10  // Y offset: -front +behind [the nozzle]
#define Z_PROBE_OFFSET_FROM_EXTRUDER 0   // Z offset: -below +above  [the nozzle]
#define MIN_PROBE_EDGE 10
#define XY_PROBE_SPEED 8000
#define Z_PROBE_SPEED_FAST HOMING_FEEDRATE_Z
#define Z_PROBE_SPEED_SLOW (Z_PROBE_SPEED_FAST / 2)
#define Z_CLEARANCE_DEPLOY_PROBE   10 // Z Clearance for Deploy/Stow
#define Z_CLEARANCE_BETWEEN_PROBES  5 // Z Clearance between probe points
#define Z_CLEARANCE_MULTI_PROBE     5 // Z Clearance between multiple probes
#define Z_PROBE_LOW_POINT          -2 // Farthest distance below the trigger-point to go before stopping
#define Z_PROBE_OFFSET_RANGE_MIN -20
#define Z_PROBE_OFFSET_RANGE_MAX 20
#define X_ENABLE_ON 0
#define Y_ENABLE_ON 0
#define Z_ENABLE_ON 0
#define E_ENABLE_ON 0 // For all extruders
#define DISABLE_X false
#define DISABLE_Y false
#define DISABLE_Z false
#define DISABLE_E false // For all extruders
#define DISABLE_INACTIVE_EXTRUDER true // Keep only the active extruder enabled.
#define INVERT_X_DIR false
#define INVERT_Y_DIR true
#define INVERT_Z_DIR false
#define INVERT_E0_DIR true
#define INVERT_E1_DIR false
#define INVERT_E2_DIR false
#define INVERT_E3_DIR false
#define INVERT_E4_DIR false
#define X_HOME_DIR -1
#define Y_HOME_DIR 1
#define Z_HOME_DIR  0
#define X_HOME_DISABLE false
#define Y_HOME_DISABLE true
#define Z_HOME_DISABLE false
#define X_BED_SIZE 225
#define Y_BED_SIZE 247
#define X_MIN_POS 0
#define Y_MIN_POS 0
#define Z_MIN_POS 0
#define X_MAX_POS X_BED_SIZE
#define Y_MAX_POS Y_BED_SIZE
#define Z_MAX_POS 99999999
#define MIN_SOFTWARE_ENDSTOPS
  #define MIN_SOFTWARE_ENDSTOP_X
  #define MIN_SOFTWARE_ENDSTOP_Y
  #define MIN_SOFTWARE_ENDSTOP_Z
#define MAX_SOFTWARE_ENDSTOPS
  #define MAX_SOFTWARE_ENDSTOP_X
  #define MAX_SOFTWARE_ENDSTOP_Y
  #define MAX_SOFTWARE_ENDSTOP_Z
#define HOMING_FEEDRATE_XY (30*60)
#define HOMING_FEEDRATE_Z  (80*60)
#define EEPROM_CHITCHAT   // Give feedback on EEPROM commands. Disable to save PROGMEM.
#define HOST_KEEPALIVE_FEATURE        // Disable this if your host doesn't like keepalive messages
#define DEFAULT_KEEPALIVE_INTERVAL 2  // Number of seconds between "busy" messages. Set with M113.
#define BUSY_WHILE_HEATING            // Some hosts require "busy" messages even during heating
#define PREHEAT_1_TEMP_HOTEND 210
#define PREHEAT_1_TEMP_BED     0
#define PREHEAT_1_FAN_SPEED     0 // Value from 0 to 255
#define PREHEAT_2_TEMP_HOTEND 240
#define PREHEAT_2_TEMP_BED    110
#define PREHEAT_2_FAN_SPEED     0 // Value from 0 to 255
#define NOZZLE_PARK_FEATURE
  #define NOZZLE_PARK_POINT { (X_MIN_POS + 20), (Y_MIN_POS + 20), 5}
  #define NOZZLE_PARK_XY_FEEDRATE 50   // X and Y axes feedrate in mm/s (also used for delta printers Z axis)
  #define NOZZLE_PARK_Z_FEEDRATE 2      // Z axis feedrate in mm/s (not used for delta printers)
#define PRINTJOB_TIMER_AUTOSTART
#define LCD_LANGUAGE en
#define DISPLAY_CHARSET_HD44780 JAPANESE
#define SDSUPPORT
#define ENCODER_STEPS_PER_MENU_ITEM 1
#define REVERSE_ENCODER_DIRECTION
#define INDIVIDUAL_AXIS_HOMING_MENU
#define REPRAP_DISCOUNT_FULL_GRAPHIC_SMART_CONTROLLER
#define SOFT_PWM_SCALE 0
#define SERVO_DELAY { 300 }

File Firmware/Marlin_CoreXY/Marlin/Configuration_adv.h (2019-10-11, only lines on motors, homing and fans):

#define E0_AUTO_FAN_PIN -1
#define E1_AUTO_FAN_PIN -1
#define E2_AUTO_FAN_PIN -1
#define E3_AUTO_FAN_PIN -1
#define E4_AUTO_FAN_PIN -1
#define CHAMBER_AUTO_FAN_PIN -1
#define X_HOME_BUMP_MM 5
#define Y_HOME_BUMP_MM 5
#define Z_HOME_BUMP_MM 5
#define HOMING_BUMP_DIVISOR { 2, 2, 4 }  // Re-Bump Speed Divisor (Divides the Homing Feedrate)
#define HOME_X_BEFORE_y
#define MICROSTEP_MODES { 16, 16, 16, 16, 16 } // [1,2,4,8,16]
#define DIGIPOT_I2C_MOTOR_CURRENTS { 1.0, 1.0, 1.0, 1.0, 1.0, 1.0, 1.0, 1.0 }  //  AZTEEG_X3_PRO
#define ADVANCED_PAUSE_FEATURE
  #define ADVANCED_PAUSE_PURGE_FEEDRATE        3  // (mm/s) Extrude feedrate (after loading). Should be slower than load feedrate.
  #define ADVANCED_PAUSE_PURGE_LENGTH         50  // (mm) Length to extrude after loading.

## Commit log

2019-10-11 Create Bed
2019-10-11 Firmware
    A modified version of the Marlin firmware.
    [Configuration.h, Configuration_adv.h]
2020-05-23 Added missing files
    [Back.stl, ControllerBox_Bottom.dxf, ControllerBox_Front_Display.dxf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]

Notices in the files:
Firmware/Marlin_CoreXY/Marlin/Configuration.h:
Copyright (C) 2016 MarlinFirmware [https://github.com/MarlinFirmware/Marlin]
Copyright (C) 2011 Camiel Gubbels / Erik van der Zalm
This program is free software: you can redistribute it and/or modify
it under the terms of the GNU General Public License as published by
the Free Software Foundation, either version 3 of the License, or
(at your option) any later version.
